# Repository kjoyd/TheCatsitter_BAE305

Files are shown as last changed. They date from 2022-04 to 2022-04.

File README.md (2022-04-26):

# TheCatsitter_BAE305
This is the documentation and Online Design profile for the BAE 305 semester design project. Group Members: Rebecca Deason, Kaitlyn Duncan, Elizabeth Howard, Lauren Doyle, Colby Redding 

# Summary
For the BAE 305 group project, the CatSitter was invented. The CatSitter is a consumer good that allows cat owners to be at ease when gone for long periods of time during the day and even on vacation, knowing that their pet is holistically taken care of. The device is an automated pet feeder that dispenses a specified amount of food at timed intervals during the day (owners can chose 1/2 cup or full cup to be dispensed every 12 hours by pressing a blue or red button). This mechanism utilizes servo motors and a 3D printed structure that holds kibble. In addition to feeding your pet, the device has a treat function where you can give your pet extra love by sending treats at timed intervals (every 2 hours) which uses a similar dispensing design mechanism with a servo motor as the feeder just at a much smaller scale. There is also a play function at timed intervals (every 3 hours) where the device utilizes two servo motors to move a laser around in different planes of motion for a cat to chase for enrichment and physical activity. These three functions and their mechanisms along with circuitry that has code loaded and the power source of battery packs are enclosed in a box designed with openings for only what the cat needs to be in contact with. A scrum agile sprint method was used throughout the semester to track goals and progress on this project to ensure completion and success. 
# Design Description

## Materials used: 

-	3- 1'x2' ¼” birch plywood sheets 
-	500g of Various colors of PLA 
-	10- sticks of Hot melt glue
-	2- 1" diameter magnets
-	Wood glue
-	2L soda bottle 
-	Plastic disposable water bottle
-	2- 1” hinges with screws 
-	2- ¼” nut and bolts
-	Electical tape
-	2- push buttons attachable to a breadboard
-	5- mini-servos 
-	20- jumper wires
-	3- buzzers attachable to a breadboard
-	3- RedBoard Arduino controllers
-	3- 2"x3.5" breadboards
-	6" of 3M Velco tape

## Special tools used: 
-	Glue gun
-	Prusa 3D printers
-	Laser cutter
-	Bandsaw 
-	Other simple wood-working tools
-	A ruler/measurement devices

## Mechanic Design:

### 3D Printed parts assembly
The basis of this design was based on a gravity feeder with servo arm controlling the amount of food that would exit the feed holder. This piece of design will be how food is measured and is controlled by a delay. To execute this design, many specific pieces where designed. The mechanic design was 3D modeled using OnShape online. There were 6 parts that were designed and modeled by hand. There include: 
1.	The feed dispenser
2.	The treat dispenser
3.	The food holder base
4.	3 rotating plates 

All the STL files can be accessed in the Github repository. All of these parts were 3D printed using PLA on the Prusa 3D printers. The tubes both are complicated round designs that would be hard to 3D print like normal, so the pieces were sliced in half to print both sides separately and be attached with glue and a ¼” nut and bolt through the flange section. 

The dispenser part is the main part of this design. The tube piece is that base that has 3 parts attached to it. This assembly rendering illustrates how this is connected.
Assembly 1

Inside the food dispenser tube, a 1" 0.156" deep magnet can be placed in the hole cutout once the 2 halves are attached to each other. 

The treat dispenser works the same as the food dispenser but on a smaller and similar scale. The treat plate fills in the slot in the treat dispenser and has the same functionality as the food feeder. An image of this assembly can be seen below. Additionally, the whole small water bottle was used. The top had the center cut out but the screw sides still in tack, and that piece would glue into the tube enough so the water bottle could fulling screw into place. About 1” down from the top of the water bottle was cut almost 80% around, leaving a bit connected to have the top still attached to the bottle. This bottle will act as the treat holder.
Assembly 2 (1)
The food holder is attached similarly, but slightly different. The base was 3D printed to have a 2L attach to it and a magnet in the round cut out on the flat edge. A 1" magnet of depth 0.156" was hot met glued into this slot. A 2L had 2 inches from the opening of the bottle removed and 0.5" slots cut vertically fron this cut. These edges were seperated out and hot melt glued onto the base piece. The bottom of the bottle was completely cut off about 4" down. This will be used as a top, but is now removable. Then 4 pea-sized glue nubs were melted into place to secure the top. 

The plates were designed to attach perfectly onto the head of the servo and be attached to the side of the treat dispenser and the food dispenser via glue and tape to secure them into place. They were attached in a way that would not inhibit the movement of the plate in any way and were sitting in the slot of their designated design. 

### Box Assembly
A box constructed of ¼” birch plywood. A design was created in Illustrator to be exported to the laser cutter to laser cut the wood. Other types of wood and plywood can be used but be careful as most woods do not work well in the laser cutter due to fumes and unsafe materials being burnt. 

The box was constructed of 2 12”x8” sides, a 12”x8.5” base, a front and back of 8”x8”, a top consisting of 3 pieces that are connected with a hinge, and a middle 8”x8” piece that holds that adds structure to the feeder. The illustration below shows the design of the box. All pieces were attached using standard wood glue and clamps to hold the pieces together while they dry. The middle section and the top were not added until later to ensure all the 3D printed pieces were in place. 

Once the box was constructed, the 3D printed parts could be attached. The food dispenser tube could be attached with hot melt glue to the front piece along with the middle piece, wedging both sides into it. The front of the tube should fit flush with the front wood piece. Now what this piece is in place, the top can be assembled on top using wood glue and clamps. These pieces were spaced out and attached in the same way they are designed in the Illustrator file. 
To attach the treat dispenser, the piece was glued to fit flush into the circular hole cut out in the left side piece. The top was also glued to the top sectional piece, with the hole matching up with the slot in the treat dispenser. 

### Laser Pointer Assembly
The laser pointer was created with 2 mini servos, one controlling x- and y-axis and another servo attached to the first servo in the side controlling the z-axis of the laser pointer. The pointer is placed on the servo arm of the z-axis servo. This laser pointer is attached with electrical tape. The z-servo is attached to the xy-servo moving arm with hot melt glue. The xy-servo was attached via a 3D printed part found online. This STL file can be found in the model files labeled “laser_case”. The servo was glued to this case and the case was glued onto the left side of the box wall at about 2” in with the top of the servo case flush with the top of the box. There should be nothing inhibiting movement of either of the servo arms. 

A breadboard with the 2 control buttons was placed in the rectangle cutout on the right side of the box. This hole was covered by tape so only the two buttons were visible and accessible. Other 2 breadboard and Arduino controllers were attached to the sides of the box using 3M Velco tape and electrical tape. All wires for each board were bundled together and extended using electrical tape. 

Both bottles should be removable, and the box can optionally be painted. We painted our pet-friendly black and attached fun charms to bling it up. But this is purely cosmetic and completely optional. 

## Circuit Design 

### Cat Feeder code summary:
In the Cat feeder code, there is an if else loop. The first loop is run when the red button(button1) is pressed. When going through the first loop the first servo opens for 2 milliseconds which releases about XX cup of food into the holding department then shuts. The second servo opens for several seconds allowing for all the food to be released into the bowl and shuts the servo gate back. A buzzer then goes off for one second alerting the cat there is food in the bowl. The if else loops have the process as the if loop, but with different time amount for the first servo to open. In this loop the gate is open for 5 milliseconds allowing for XX cups to be dropped. Both the if and if else loop repeat every12 hours to feed the cat. The else loop is for when neither button is pressed and keeps both servos in the closed position until one button is pressed. 

### Treat code summary:  

The treat dispenser code is very similar to that of the food dispenser but only uses one servo. A speaker alerts the cat treats are about to drop then opens a servo for 2 milliseconds releasing a few treats then closes back and waits 2 hours before releasing more treats.  

### Laser Code Summary:

The void loop in the laser code has a list of different servo positions that move each servo to a different location when the laser is on and holds a position for a certain amount of time before moving again. There is also a buzzer hooked up to the circuit that plays a different sound than the treat and food dispenser to alert the cat that it is time to play with the laser. 

# Discussion of Design
### Measuring Design
There is a lot that goes into this device. The main food drop mechanism is one that is based off of gravity. This system uses the speed of a servo arm to precisely measure the amount of food that the pet is given access to. The servo is normally closed, held to the bottom of the container of food. When food is dispensed, the servo opens the opening based on a delay to allow food through. This amount can vary based on the delay set in the code for the servo arm. The amount dropped will vary from example to example, so the delay in the code is specific to this design to measure what is desired. If the same design is used with the same parts, this should replicate perfectly. The benefit of this mechanism is that it is easy to control and has the preciseness for our needs. This feeder does not need to be extremely precise. The food should be within a 1/16th of a cup, and this system allows for that much precision. This design could improve in precision by using stronger and more precise motors. 

Another servo is attached to the front plate for the food to sit in that slot until it is time to deliver the food. This servo is designed to stay closed and open when the food from the measuring plate is dropped in the tube. This arm rotates about 10 seconds after the food is dispensed. This system was designed with cat psychology in mind. If the cat got used to hearing the first arm going off, they may get too excited and attack the machine since the food has not come out yet. With the second arm, the cat will not attack the machine since that second arm they will associate with food rather than the first one. This also makes the design more insect repellent by having an extra boundary between the environments and the food. 

The treat feeder was designed in a similar way. The design is simpler by not including a base servo to control when the tube is open of closed. This makes for a better design, as the base plate would be overkill on such a small part and would not fit nicely into the box. 

### Model design
The models were designed to be custom for this object. Each plate was designed to be thin and fit snuggly on the end of the servo to create a simple design. These are modeled to include a bevel to be more accurate in movement, and much smaller than the slot size to avoid friction which can greatly affect the efficiency of the servo.

The tubes were designed with attachment to the box in mind. The base tube is designed to sit in the wall of the box, hence the small horizontal section at the bottom of the tube. This design helps with stability of the piece and creates a more cohesive product. The custom design includes a top section that holds the base of the food holder. This part includes a lip that the holder fits into along with a magnet that lines up with a magnet on the food holder base. This magnet helps with the stability of the part and will avoid being turned over by the cat. The tube also has a base of an L-bracket. This bracket also assists in stability of the product and rests on a small piece of wood glued into place. The advantage of this design is that it is very specific yet simple. Each piece fits perfectly into place and is designed for that very purpose. This allows for a very fluid design that looks good and functions even better. 

# Testing Description

# Discussion of Testing

# Testing Results

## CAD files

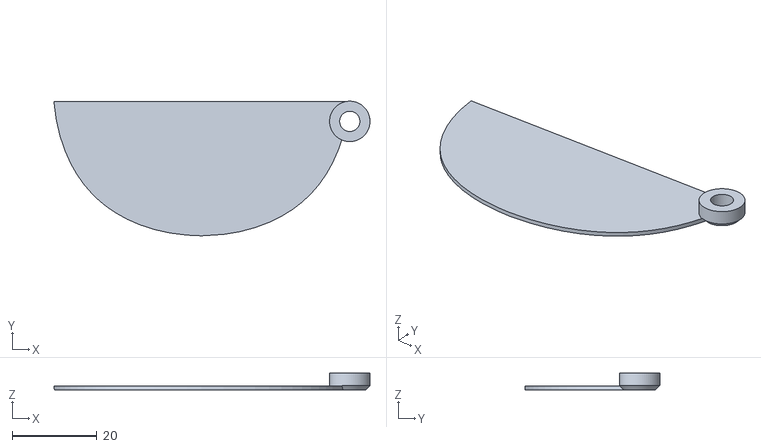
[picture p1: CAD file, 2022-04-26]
3D Model STL Files/measuring_plate.stl
74.4 x 31.7 x 3.97

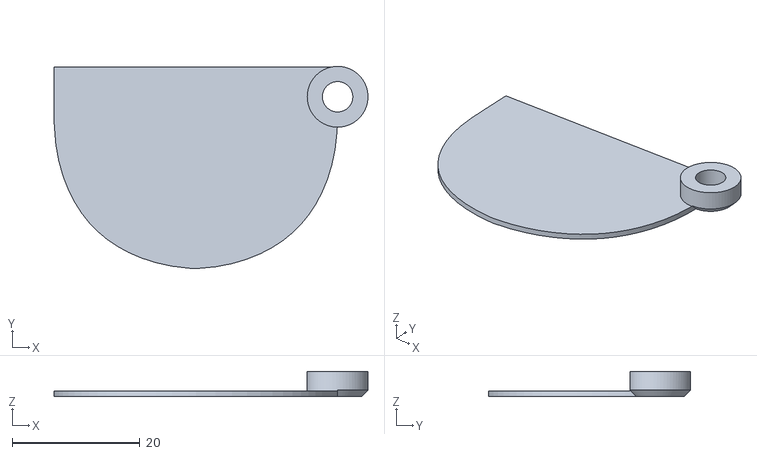
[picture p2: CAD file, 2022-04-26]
3D Model STL Files/treat_plate.stl
49.2 x 31.7 x 3.97

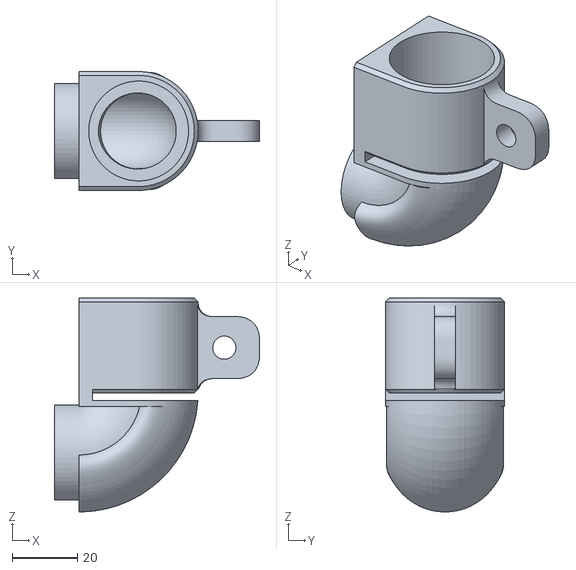
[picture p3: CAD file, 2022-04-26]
3D Model STL Files/treat_dispenser_tube.stl
63.0 x 36.5 x 65.7

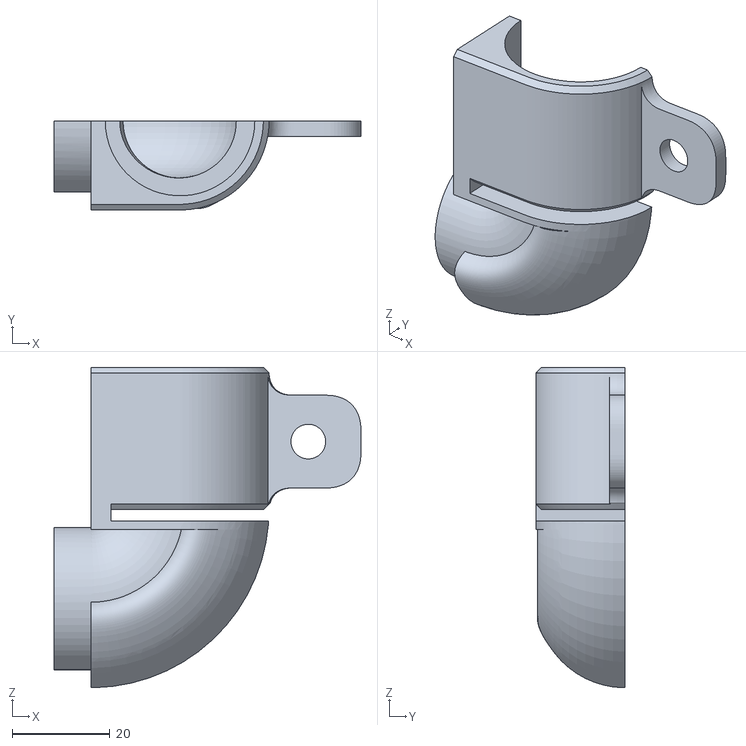
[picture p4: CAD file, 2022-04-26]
3D Model STL Files/treat_tube_ff_right.stl
63.0 x 18.3 x 65.7

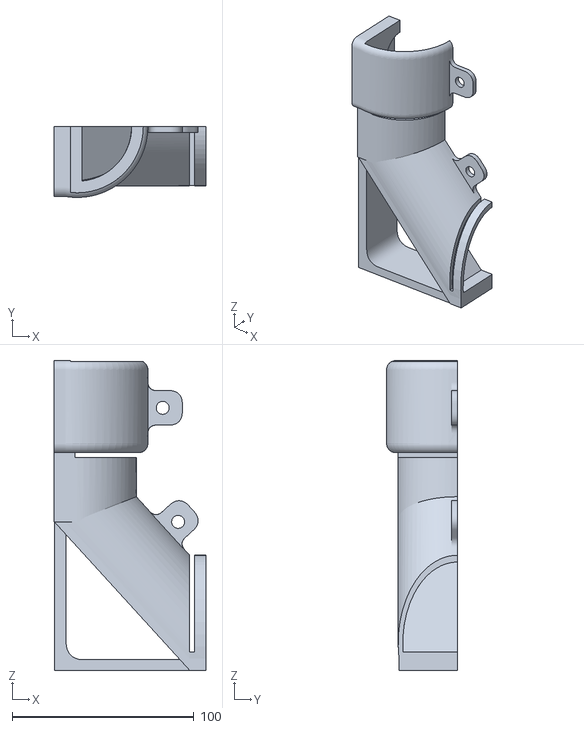
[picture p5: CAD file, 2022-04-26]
3D Model STL Files/food_tube_ff_left.stl
83.6 x 39.0 x 170.8

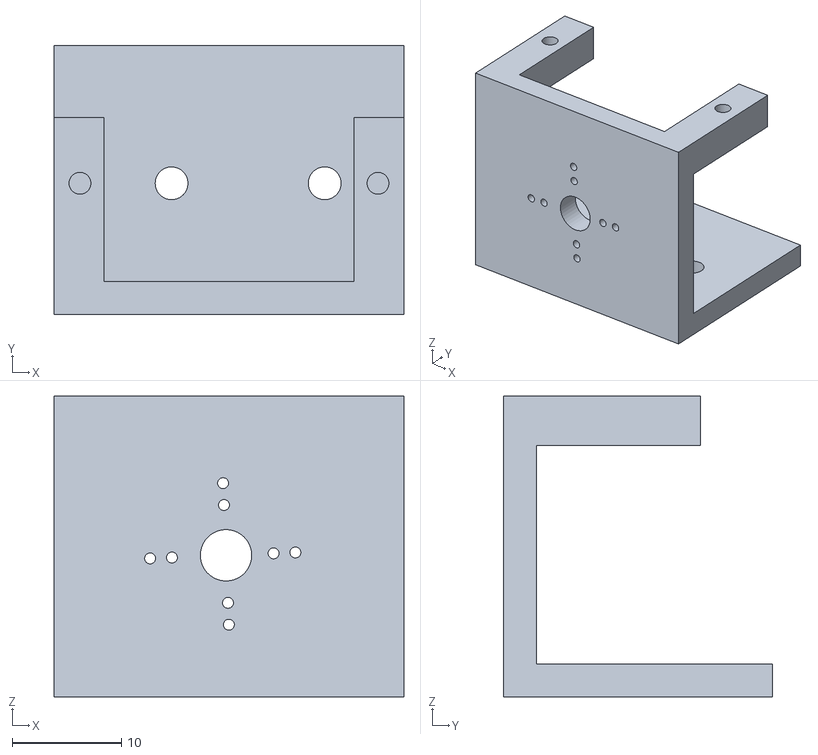
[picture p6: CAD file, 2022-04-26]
3D Model STL Files/laser_case.STL
32.0 x 24.6 x 27.5

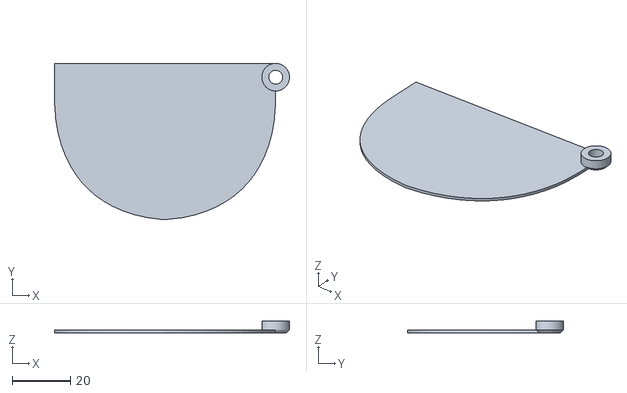
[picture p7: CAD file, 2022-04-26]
3D Model STL Files/base_plate_food dispenser.stl
81.0 x 53.8 x 3.97

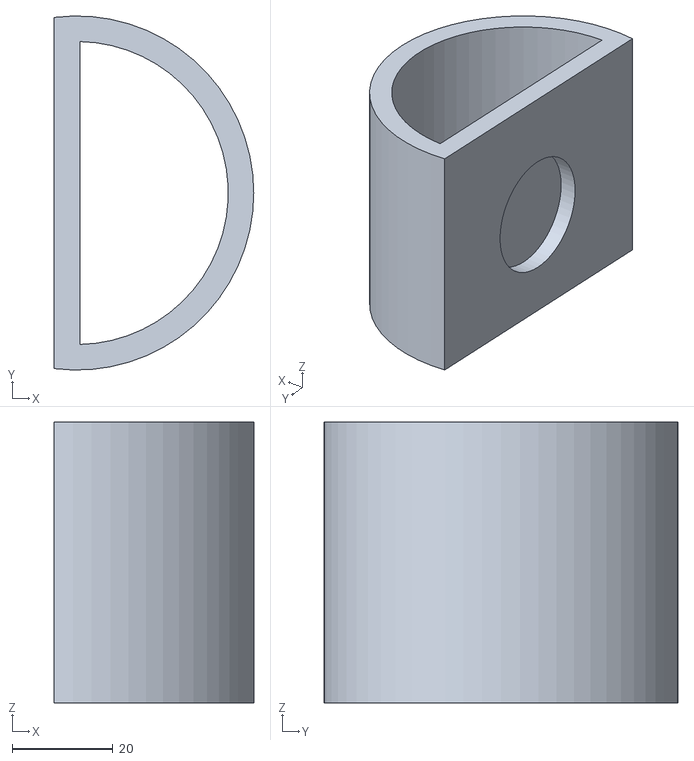
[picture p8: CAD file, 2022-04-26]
3D Model STL Files/food_holder_base.stl
39.7 x 70.4 x 55.9

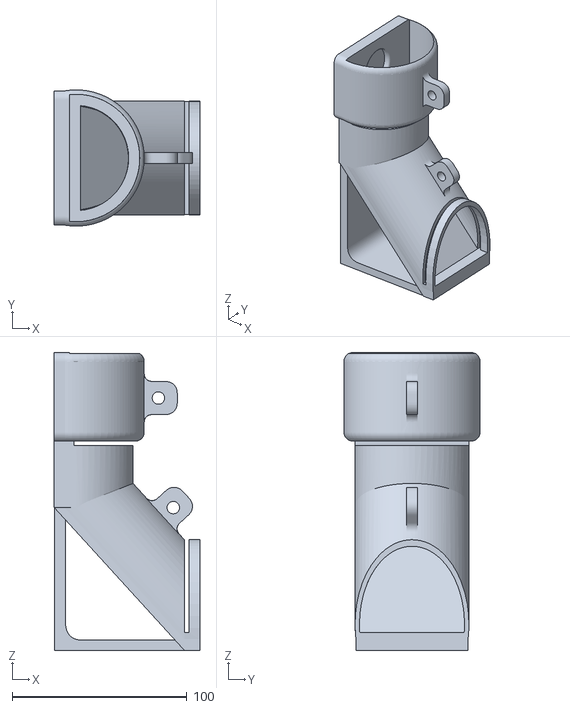
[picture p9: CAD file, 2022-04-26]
3D Model STL Files/food_dispenser_tube.stl
83.6 x 78.1 x 170.8

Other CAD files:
3D Model STL Files/food_tube_ff_right.stl
3D Model STL Files/treat_tube_ff_left.stl

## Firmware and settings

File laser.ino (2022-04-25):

#include<Servo.h> //includes servo motors

Servo Myservo1;
Servo Myservo2;
int buzzer=11;
int laserPin=6;
//initializes all variablee and pins

void setup() {
  Myservo1.attach(10);
  Myservo2.attach(9);
  pinMode(buzzer, OUTPUT);
  pinMode(laserPin, OUTPUT);
  //initalizes input and ouputs 
}

void loop() {
  // put your main code here, to run repeatedly:
  digitalWrite(laserPin, HIGH); // turns laser one
  tone(buzzer,62);        //speaker on to alert cat
  delay(100);             //pause
  noTone(buzzer);         // turns speaker off
  Myservo1.write(120);     //writes servo to new position
  Myservo2.write(100);    //writes servo to new position
  delay(1000);            //pause
  Myservo1.write(90);     //writes servo to new position
  Myservo2.write(70);     //writes servo to new position
  delay(2000);            //pause
  Myservo2.write(115);     //writes servo to new position
  delay(2000);            //pause
  Myservo2.write(20);     //writes servo to new position
  delay(2000);            //pause
  Myservo1.write(90);     //writes servo to new position
  Myservo2.write(150);     //writes servo to new position
  delay(2000);            //pause
  Myservo1.write(125);     //writes servo to new position
  Myservo2.write(90);     //writes servo to new position
  delay(1000);            //pause
  Myservo1.write(45);     //writes servo to new position
  Myservo2.write(140);     //writes servo to new position
  delay(2000);            //pause
  Myservo2.write(100);    //writes servo to new position
  Myservo1.write(70);     //writes servo to new position
  delay(2000);            //pause
  Myservo2.write(50);     //writes servo to new position
  delay(2000);            //pause
  Myservo1.write(32);     //writes servo to new position
  Myservo2.write(130);     //writes servo to new position
  delay(2000);            //pause
  Myservo1.write(80);     //writes servo to new position
  Myservo2.write(90);    //writes servo to new position
  delay(1000);            //pause
  Myservo1.write(25);     //writes servo to new position
  Myservo2.write(155);     //writes servo to new position
  delay(2000);            //pause
  Myservo2.write(75);     //writes servo to new position
  Myservo1.write(65);     //writes servo to new position
  Myservo2.write(135);     //writes servo to new position
  delay(2000);            //pause
  Myservo1.write(90);     //writes servo to new position
  Myservo2.write(95);     //writes servo to new position
  delay(2000);            //pause
  Myservo1.write(70);     //writes servo to new position
  Myservo2.write(120);     //writes servo to new position
  delay(1000);            //pause
  Myservo1.write(20);     //writes servo to new position
  Myservo2.write(80);     //writes servo to new position
  delay(2000);            //pause
  Myservo2.write(140);     //writes servo to new position
  Myservo1.write(70);     //writes servo to new position
  Myservo2.write(90);     //writes servo to new position
  delay(2000);            //pause
  Myservo1.write(55);     //writes servo to new position
  Myservo2.write(140);     //writes servo to new position
  delay(2000);            //pause
  digitalWrite(laserPin, LOW); //turns laser off
  delay(10000); //waits X time until laser comes back on
}

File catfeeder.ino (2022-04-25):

#include<Servo.h> //includes servo motors
Servo Myservo1;
Servo Myservo2;
int button = 5;
int button1 = 3;
int buzzer=11;

//initializes all variablee and pins
void setup()
{
  pinMode(button,INPUT_PULLUP);
  pinMode(button1,INPUT_PULLUP);
  Myservo1.attach(10);
  Myservo2.attach(9);
  pinMode(buzzer, OUTPUT);
  //initalizes input and ouputs 
}

void loop(){
  
  if(digitalRead(button)==LOW){ //if button 1 presses
    Myservo2.write(80);         //opens gate
    delay(200);                 //gate open for 2 ms
    Myservo2.write(20);         //close gate
    delay(1000);                //waits 1 second between closing servo 2 and opening servo 1
    Myservo1.write(40);         //opens gate
    delay(1000);                //gate open for 1 s
    Myservo1.write(100);        //close gate
    tone(buzzer,262);           //speaker on to alert cat
    delay(1000);                //keeps speaker on for 1 second
    noTone(buzzer);             // turns speaker off
    delay(5000);                //waits x time until time to feed agai
    Myservo2.write(80);         //opens gate
    delay(200);                 //gate open for 2 ms
    Myservo2.write(20);         //close gate
    delay(1000);                //waits 1 second between closing servo 2 and opening servo 1
    Myservo1.write(40);         //opens gate
    delay(1000);                //gate open for 1 s
    Myservo1.write(100);        //close gate
    tone(buzzer,262);           //speaker on to alert cat
    delay(1000);                //keeps speaker on for 1 second
    noTone(buzzer);             // turns speaker off

    
  }
  else if(digitalRead(button1)==LOW){
    Myservo2.write(80);         //opens gate
    delay(500);                 //gate open for 5 ms
    Myservo2.write(20);         //close gate
    delay(2000);                //waits 2 second between closing servo 2 and opening servo 1
    Myservo1.write(40);         //opens gate
    delay(2000);                //gate open for 2s
    Myservo1.write(100);        //close gate
    tone(buzzer,262);           //speaker on to alert cat
    delay(1000);                //keeps speaker on for 1 second
    noTone(buzzer);             // turns speaker off
    delay(5000);                //waits x time until time to feed again
    Myservo2.write(80);         //opens gate
    delay(500);                 //gate open for 5 ms
    Myservo2.write(20);         //close gate
    delay(2000);                //waits 1 second between closing servo 2 and opening servo 1
    Myservo1.write(40);         //opens gate
    delay(2000);                //gate open for 2s
    Myservo1.write(100);        //close gate
    tone(buzzer,262);           //speaker on to alert cat
    delay(1000);                //keeps speaker on for 1 second
    noTone(buzzer);             // turns speaker off
    
  }
  else { //servo doesnt move if no button is pressed and retturns servo to closes position
    Myservo1.write(100);
    Myservo2.write(20);
    
  }
}
